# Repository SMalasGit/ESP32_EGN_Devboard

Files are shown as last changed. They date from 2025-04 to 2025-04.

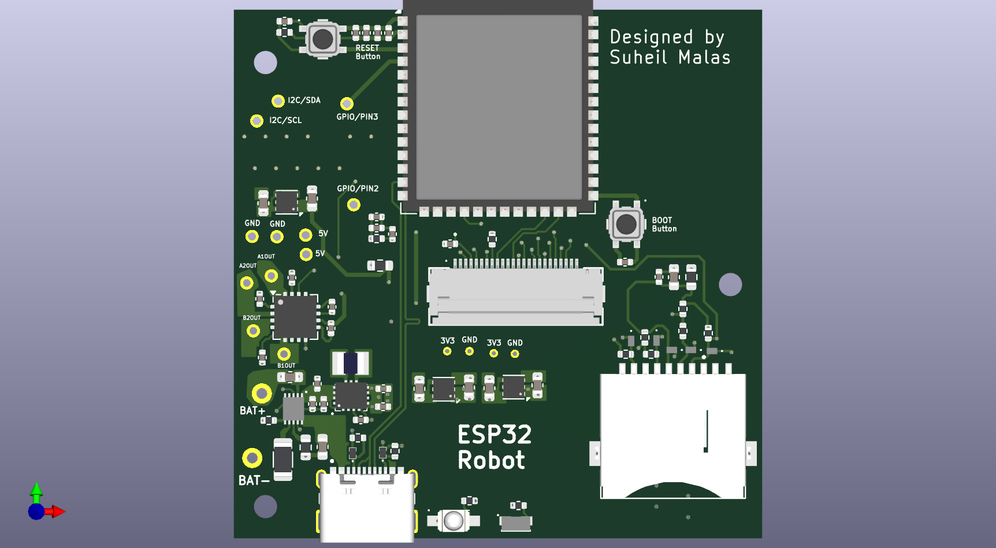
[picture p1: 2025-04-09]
ENGBOT.png

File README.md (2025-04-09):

# ESP32_EGN_Devboard
A repository for an ESP32-S3 engineering development board I designed. It houses an ESP32, a buck-boost regulator, battery charging IC with power path, two BLDC motor drivers, a microSD-interface, and a camera.

ENGBOT

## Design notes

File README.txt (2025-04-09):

This is a custom PCB for an ESP32 robot, meant to act as an educational tool for students and engineers alike. This PCB is built on 6 layers, features an ENIG finish, and uses Via-in-pad technology for compact size and function

This custom pcb has several unique features and can be combined with standard Arduino code libaries or off the shelf Epressif IDF IDE code to create a custom rover, robot, etc. This pcb features a custom lithium ion power path IC, allowing for power via USB-C, lithium ion battery, or both, depending on which power source is available. This IC also features battery protection and charging, allowing a user to know when the battery needs charging from the orange LED indicator, and when it is done charging from the green LED indicator

Furthermore, this pcb features a buck-boost regulator to allow a constant steady supply of 5 volts. In addition, this PCB includes a mosfet-based motor driver IC to control DC motors with ease. Since this board utilizes the powerful ESP32-S3 with a 240MHZ processor that includes Wifi, Bluetooth, and Zigbee, I have included a parallel camera interface connector, along with an SDIO microSD card connector. Finally, there is a series of GPIOs broken out for additional functionality, with UART and I2C capability.

Manufactured by JLCPCB standard 6 layer service.

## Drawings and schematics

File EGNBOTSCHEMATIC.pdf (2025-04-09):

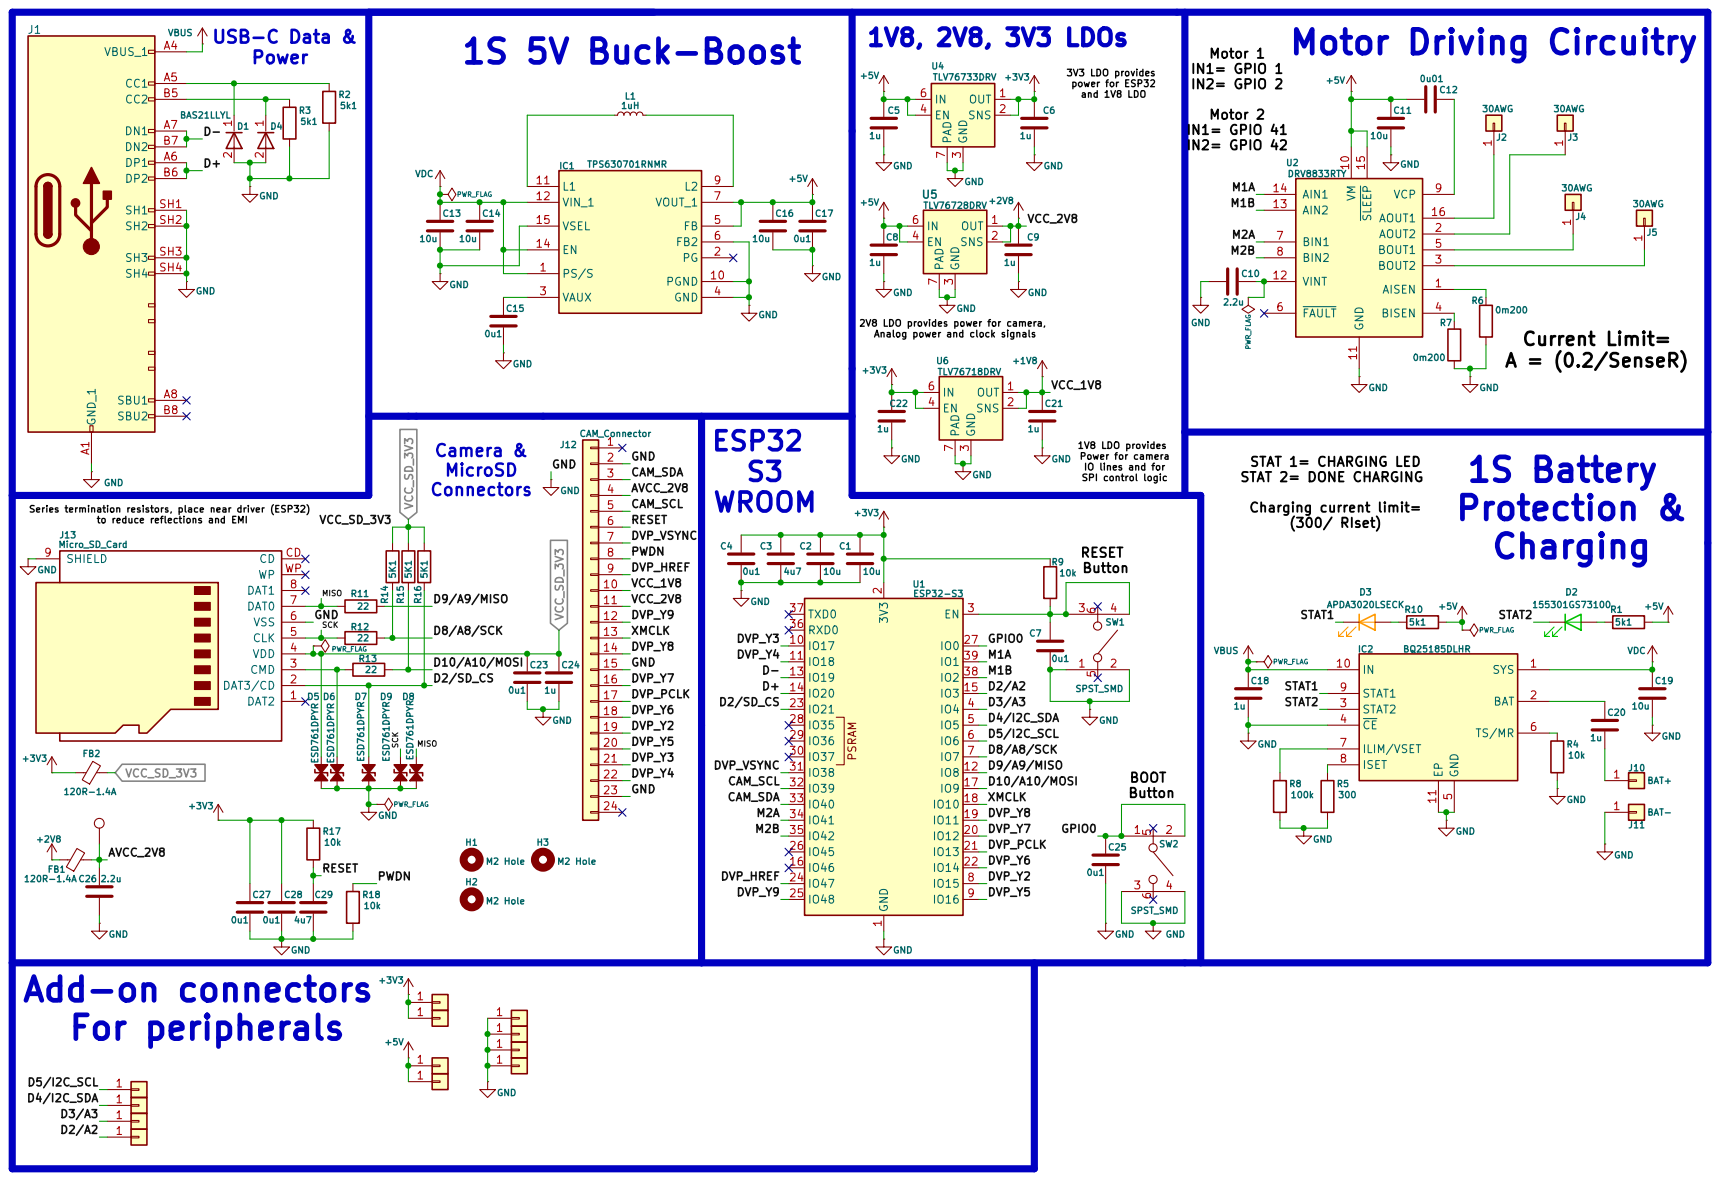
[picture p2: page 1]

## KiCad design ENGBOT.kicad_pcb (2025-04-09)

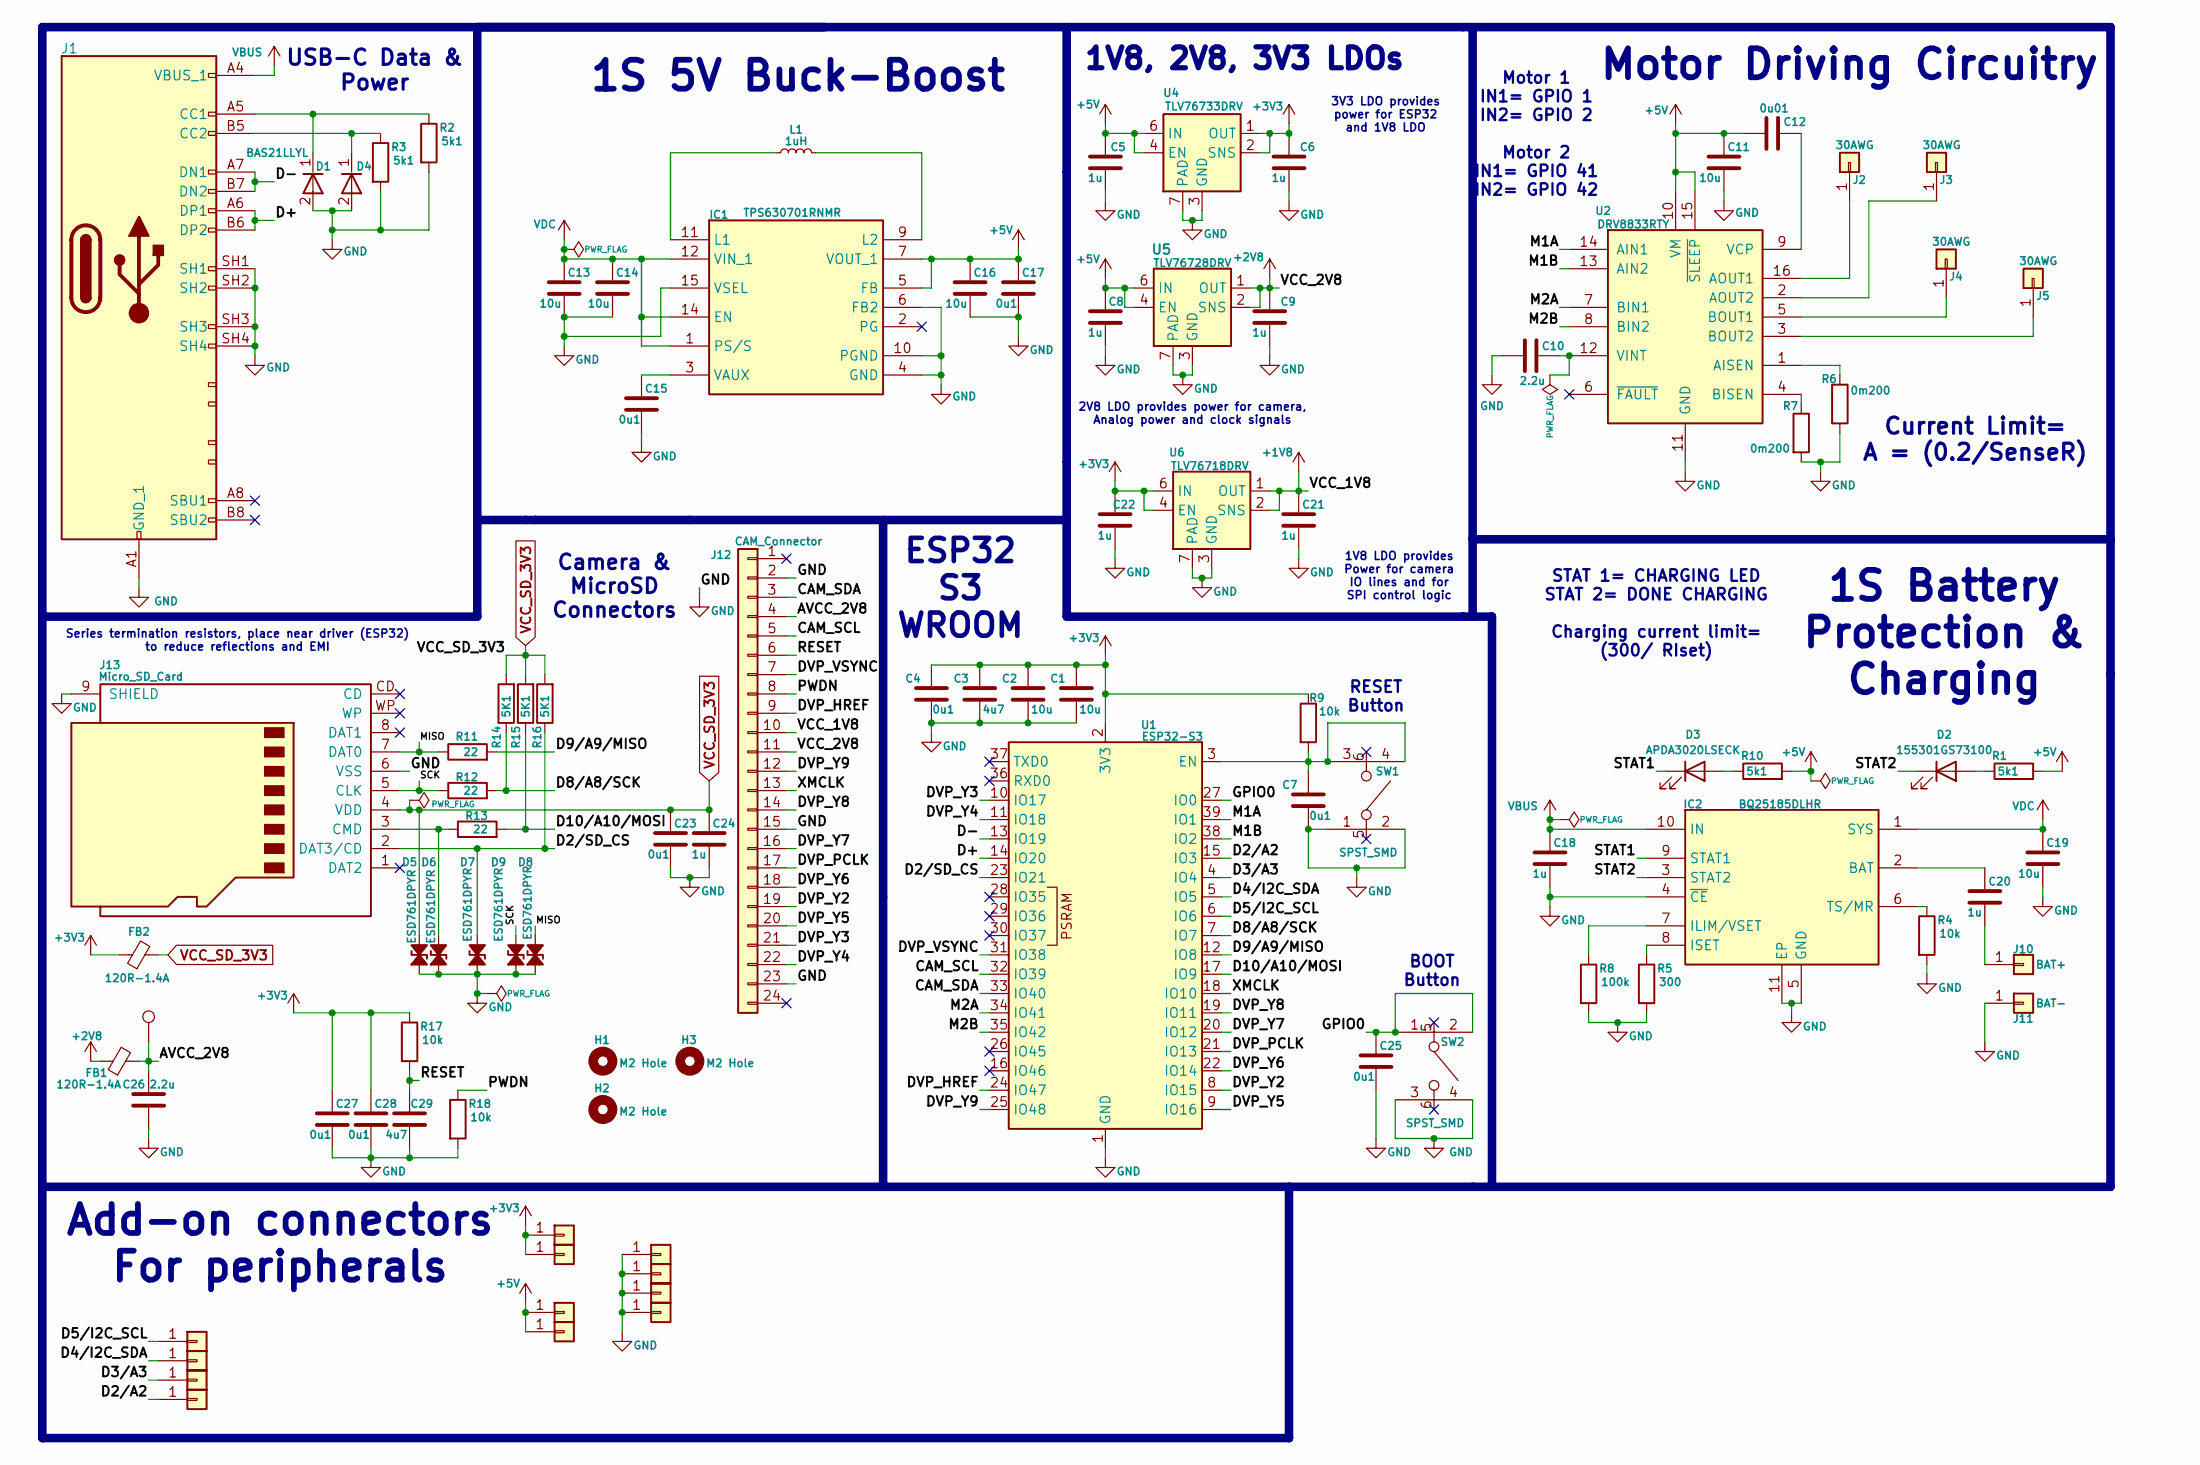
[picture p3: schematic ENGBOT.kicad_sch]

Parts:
C1, C2, C11, C13, C14, C16, C19: 10u; C_0402_1005Metric
C3, C29: 4u7; C_0402_1005Metric
C4, C7, C15, C17, C23, C25, C27, C28: 0u1; C_0402_1005Metric
C5, C6, C8, C9, C18, C20, C21, C22, C24: 1u; C_0603_1608Metric
C10, C26: 2.2u; C_0402_1005Metric
C12: 0u01; C_0402_1005Metric
D1, D4: BAS21LLYL; Mouser Part Number 771-BAS21LLYL
D2: 155301GS73100; 155301RS73100
D3: APDA3020LSECK; APDA3020LZGCK
D5, D6, D7, D8, D9: ESD761DPYR
FB1, FB2: 120R-1.4A; R_0603_1608Metric
H1, H2, H3: M2 Hole; MountingHole_2.2mm_M2_ISO7380
IC1: TPS630701RNMR; Mouser Part Number 595-TPS630701RNMR
IC2: BQ25185DLHR; SON40P220X200X80-11N; Mouser Part Number 595-BQ25185DLHR
J1: USB4215; GCT_USB4215-03-A_REVA
J2, J3, J4, J5: 30AWG; 30 AWG
J10: BAT+; BAT Wire
J11: BAT-; BAT Wire
J12: CAM_Connector; F33Z1A7Q1E8C24
J13: Micro_SD_Card; CUI_MSD-11-A
J14, J15, J16, J18, J19, J22, J23, J24, J25, J27, J28, J29: Conn_01x01; Motor Hole 30awg
L1: 1uH; INDC2520X120N
R1, R2, R3, R10: 5k1; R_0402_1005Metric
R4, R9, R17, R18: 10k; R_0402_1005Metric
R5: 300; R_0603_1608Metric
R6, R7: 0m200; C_0402_1005Metric
R8: 100k; R_1206_3216Metric
R11, R12, R13: 22; R_0402_1005Metric
R14, R15, R16: 5K1; R_0402_1005Metric
SW1, SW2: SPST_SMD; TS2134035BK160SMTTR
TP1: TestPoint; test
U1: ESP32-S3; ESP32-S3-WROOM-1
U2: DRV8833RTY; Texas_RTY_WQFN-16-1EP_4x4mm_P0.65mm_EP2.1x2.1mm_ThermalVias
U4: TLV76733DRV; WSON-6-1EP_2x2mm_P0.65mm_EP1x1.6mm_ThermalVias
U5: TLV76728DRV; WSON-6-1EP_2x2mm_P0.65mm_EP1x1.6mm_ThermalVias
U6: TLV76718DRV; WSON-6-1EP_2x2mm_P0.65mm_EP1x1.6mm_ThermalVias

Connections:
+1V8: C21.1, J12.10, U6.1 (OUT), U6.2 (SNS)
+2V8: C9.1, FB1.1, J12.11, U5.1 (OUT), U5.2 (SNS)
+3V3: C1.1, C2.1, C3.1, C4.1, C6.1, C22.1, C27.1, C28.1, FB2.1, J18.1, J19.1, R9.1, R17.1, U1.2 (3V3), U4.1 (OUT), U4.2 (SNS), U6.4 (EN), U6.6 (IN)
+5V: C5.1, C8.1, C11.1, C12.1, C16.1, C17.1, IC1.5 (FB), IC1.7 (VOUT_1), IC1.8 (VOUT_2), J24.1, J25.1, R1.2, R10.2, U2.10 (VM), U2.15 (~SLEEP), U4.4 (EN), U4.6 (IN), U5.4 (EN), U5.6 (IN)
/AVCC_2V8: C26.2, FB1.2, J12.4, TP1.1
/CAM_SCL: J12.5, U1.32 (IO39)
/CAM_SDA: J12.3, U1.33 (IO40)
/D2/A2: J14.1, U1.15 (IO3)
/D2/SD_CS: D7.2 (A2), J13.2 (DAT3/CD), R16.1, U1.23 (IO21)
/D3/A3: J29.1, U1.4 (IO4)
/D4/I2C_SDA: J28.1, U1.5 (IO5)
/D5/I2C_SCL: J27.1, U1.6 (IO6)
/D8/A8/SCK: R12.2, R14.1, U1.7 (IO7)
/D9/A9/MISO: R11.2, U1.12 (IO8)
/D10/A10/MOSI: R13.2, R15.1, U1.17 (IO9)
/D+: J1.A6 (DP1), J1.B6 (DP2), U1.14 (IO20)
/D-: J1.A7 (DN1), J1.B7 (DN2), U1.13 (IO19)
/DVP_HREF: J12.9, U1.24 (IO47)
/DVP_PCLK: J12.17, U1.21 (IO13)
/DVP_VSYNC: J12.7, U1.31 (IO38)
/DVP_Y2: J12.19, U1.8 (IO15)
/DVP_Y3: J12.21, U1.10 (IO17)
/DVP_Y4: J12.22, U1.11 (IO18)
/DVP_Y5: J12.20, U1.9 (IO16)
/DVP_Y6: J12.18, U1.22 (IO14)
/DVP_Y7: J12.16, U1.20 (IO12)
/DVP_Y8: J12.14, U1.19 (IO11)
/DVP_Y9: J12.12, U1.25 (IO48)
/GPIO0: C25.1, SW2.1 (A), SW2.2 (B), U1.27 (IO0)
/M1A: U1.39 (IO1), U2.14 (AIN1)
/M1B: U1.38 (IO2), U2.13 (AIN2)
/M2A: U1.34 (IO41), U2.7 (BIN1)
/M2B: U1.35 (IO42), U2.8 (BIN2)
/MISO: D8.2 (A2), J13.7 (DAT0), R11.1
/PWDN: J12.8, R18.1
/RESET: C29.1, J12.6, R17.2
/SCK: D9.2 (A2), J13.5 (CLK), R12.1
/STAT1: D3.1 (K), IC2.9 (STAT1)
/STAT2: D2.1 (K), IC2.3 (STAT2)
/XMCLK: J12.13, U1.18 (IO10)
GND: C1.2, C2.2, C3.2, C4.2, C5.2, C6.2, C7.2, C8.2, C9.2, C10.1, C11.2, C13.2, C14.2, C15.2, C16.2, C17.2, C18.2, C19.2, C21.2, C22.2, C23.2, C24.2, C25.2, C26.1, C27.2, C28.2, C29.2, D1.2 (A), D4.2 (A), D5.1 (A1), D6.1 (A1), D7.1 (A1), D8.1 (A1), D9.1 (A1), IC1.4 (GND), IC1.6 (FB2), IC1.10 (PGND), IC1.15 (VSEL), IC2.4 (~CE), IC2.5 (GND), IC2.11 (EP), J1.A1 (GND_1), J1.A12 (GND_2), J1.B1 (GND_3), J1.B12 (GND_4), J1.SH1, J1.SH2, J1.SH3, J1.SH4, J11.1, J12.2, J12.15, J12.23, J13.6 (VSS), J13.9 (SHIELD), J15.1, J16.1, J22.1, J23.1, R2.2, R3.2, R4.2, R5.2, R6.2, R7.2, R8.2, R18.2, SW1.1 (A), SW1.2 (B), SW2.3, SW2.4, U1.1 (GND), U1.40 (GND), U1.41 (GND), U2.11 (GND), U2.17 (GND), U4.3 (GND), U4.5 (GND), U4.7 (PAD), U5.3 (GND), U5.5 (GND), U5.7 (PAD), U6.3 (GND), U6.5 (GND), U6.7 (PAD)
unnamed: D1.1 (K), J1.A5 (CC1), R2.1
unnamed: D2.2 (A), R1.1
unnamed: D3.2 (A), R10.1
unnamed: D4.1 (K), J1.B5 (CC2), R3.1
unnamed: D6.2 (A2), J13.3 (CMD), R13.1
unnamed: IC1.11 (L1), L1.1
unnamed: IC1.9 (L2), L1.2
unnamed: C15.1, IC1.3 (VAUX)
unnamed: C20.1, IC2.2 (BAT)
unnamed: IC2.7 (ILIM/VSET), R8.1
unnamed: IC2.8 (ISET), R5.1
unnamed: IC2.6 (TS/MR), R4.1
unnamed: J2.1, U2.16 (AOUT1)
unnamed: J3.1, U2.2 (AOUT2)
unnamed: J4.1, U2.5 (BOUT1)
unnamed: J5.1, U2.3 (BOUT2)
unnamed: C20.2, J10.1
unnamed: C7.1, R9.2, SW1.3, SW1.4, U1.3 (EN)
unnamed: R6.1, U2.1 (AISEN)
unnamed: R7.1, U2.4 (BISEN)
unnamed: C12.2, U2.9 (VCP)
unnamed: C10.2, U2.12 (VINT)
VBUS: C18.1, IC2.10 (IN), J1.A4 (VBUS_1), J1.A9 (VBUS_2), J1.B4 (VBUS_3), J1.B9 (VBUS_4)
VCC_SD_3V3: C23.1, C24.1, D5.2 (A2), FB2.2, J13.4 (VDD), R14.2, R15.2, R16.2
VDC: C13.1, C14.1, C19.1, IC1.1 (PS/S), IC1.12 (VIN_1), IC1.13 (VIN_2), IC1.14 (EN), IC2.1 (SYS)

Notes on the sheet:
Motor 1 IN1= GPIO 1 IN2= GPIO 2 Motor 2 IN1= GPIO 41 IN2= GPIO 42
ESP32 S3 WROOM
1S Battery Protection & Charging
STAT 1= CHARGING LED STAT 2= DONE CHARGING Charging current limit= (300/ RIset)
2V8 LDO provides power for camera, Analog power and clock signals
Camera & MicroSD Connectors
RESET Button
1S 5V Buck-Boost
1V8 LDO provides Power for camera IO lines and for SPI control logic
Motor Driving Circuitry
USB-C Data & Power
BOOT Button
Add-on connectors For peripherals
1V8, 2V8, 3V3 LDOs
3V3 LDO provides power for ESP32 and 1V8 LDO
Current Limit= A = (0.2/SenseR)
Series termination resistors, place near driver (ESP32) to reduce reflections and EMI

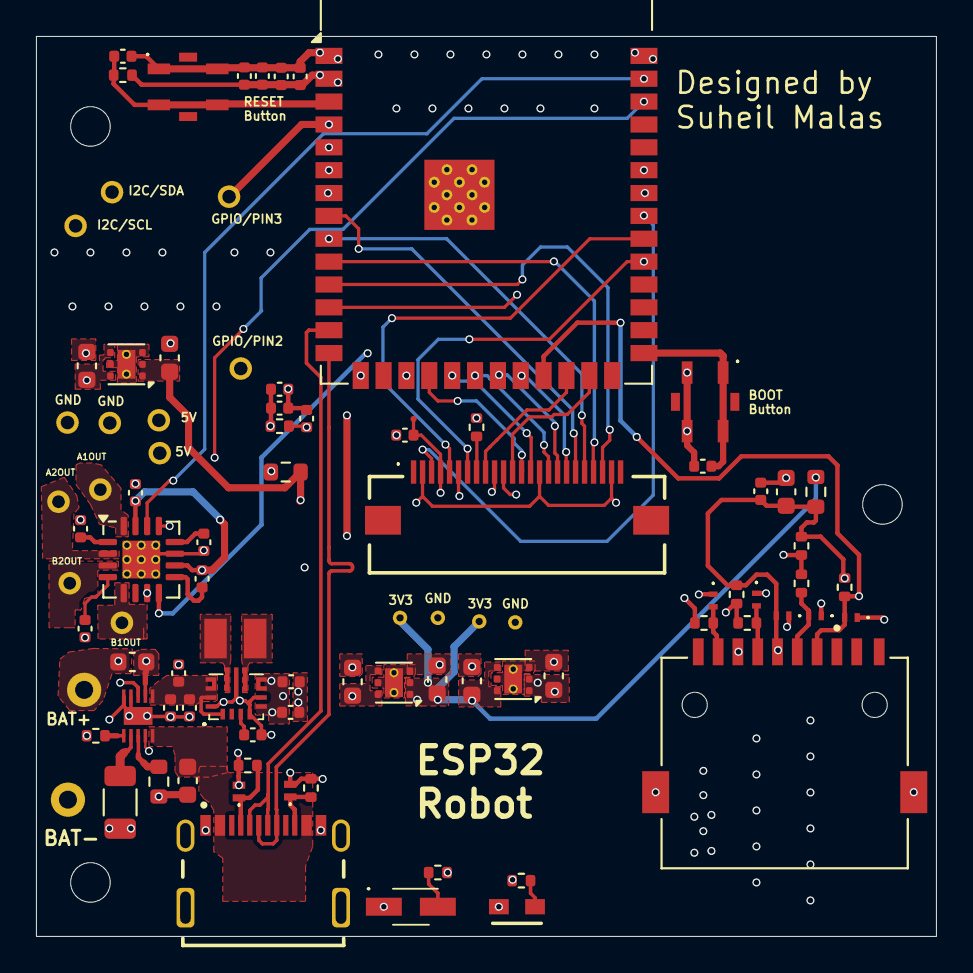
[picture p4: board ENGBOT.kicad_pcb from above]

Board: 6 copper layers, 50.0 x 50.0 mm, 93 parts (0 on the bottom side), 66 nets.
